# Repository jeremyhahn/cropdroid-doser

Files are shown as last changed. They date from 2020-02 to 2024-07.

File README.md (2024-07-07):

# cropdroid-doser

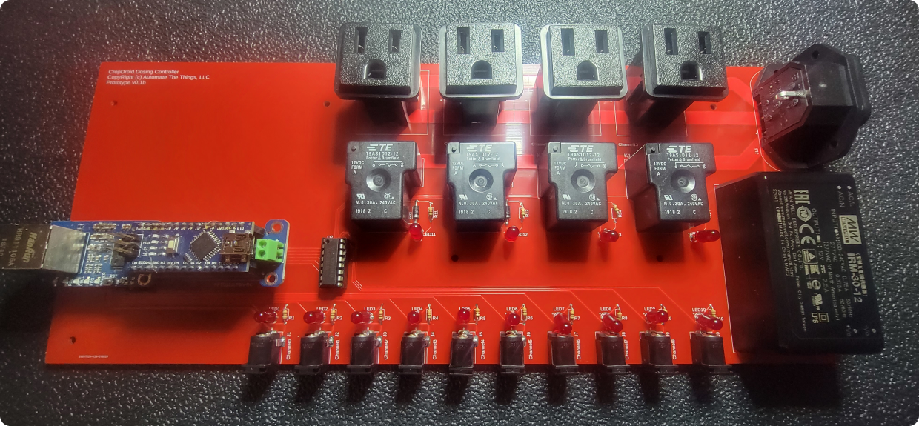
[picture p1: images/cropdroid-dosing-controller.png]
[](https://github.com/jeremyhahn/cropdroid-doser)

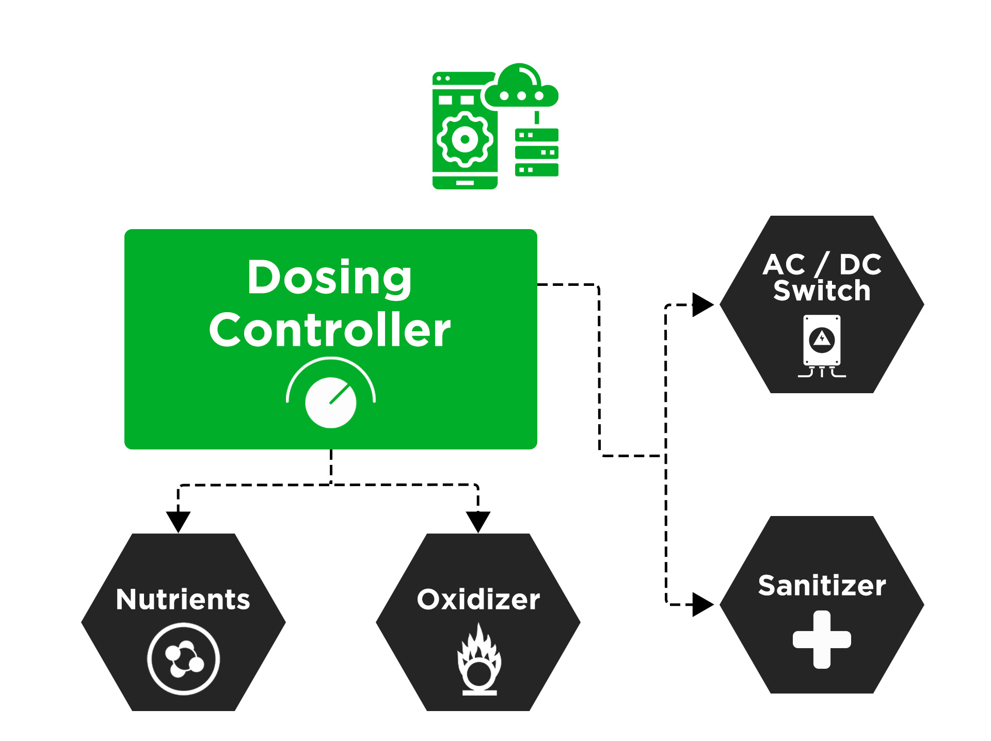
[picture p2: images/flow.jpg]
[](https://github.com/jeremyhahn/cropdroid-doser)

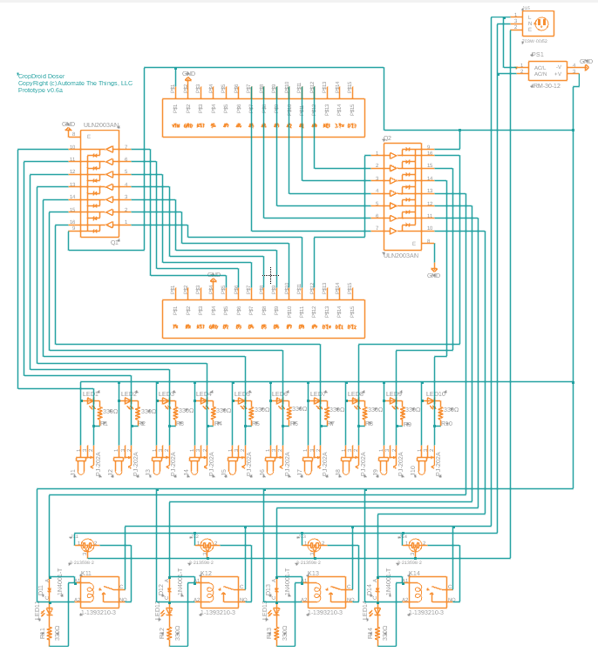
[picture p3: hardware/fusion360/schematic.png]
[](https://github.com/jeremyhahn/cropdroid-doser/blob/master/hardware/fusion360/schematic.png)

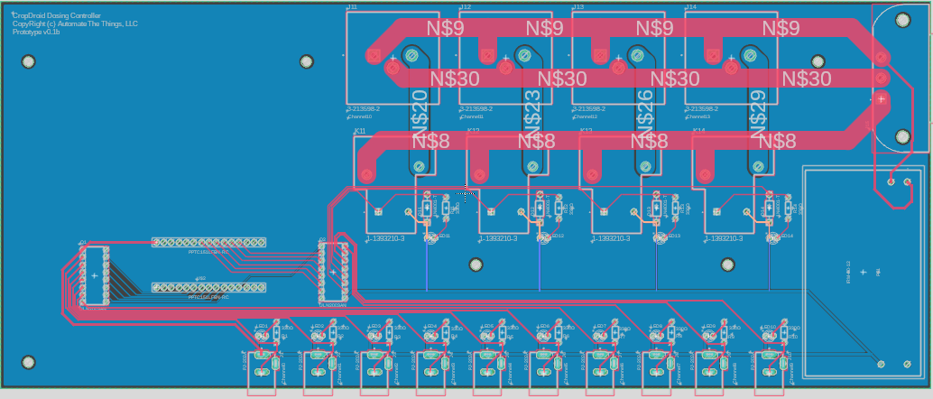
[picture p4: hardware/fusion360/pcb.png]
[](https://github.com/jeremyhahn/cropdroid-doser/blob/master/hardware/fusion360/pcb.png)

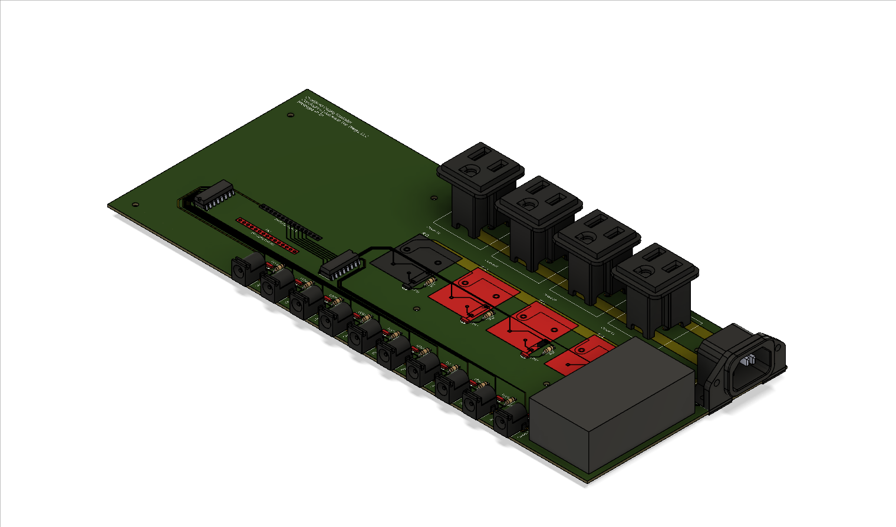
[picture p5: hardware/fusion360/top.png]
[](https://github.com/jeremyhahn/cropdroid-doser/blob/master/hardware/fusion360/top.png)

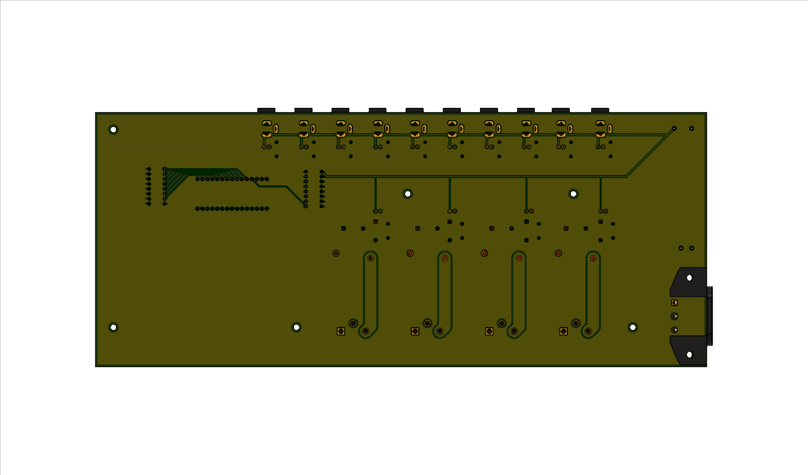
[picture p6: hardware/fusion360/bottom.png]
[](https://github.com/jeremyhahn/cropdroid-doser/blob/master/hardware/fusion360/bottom.png)

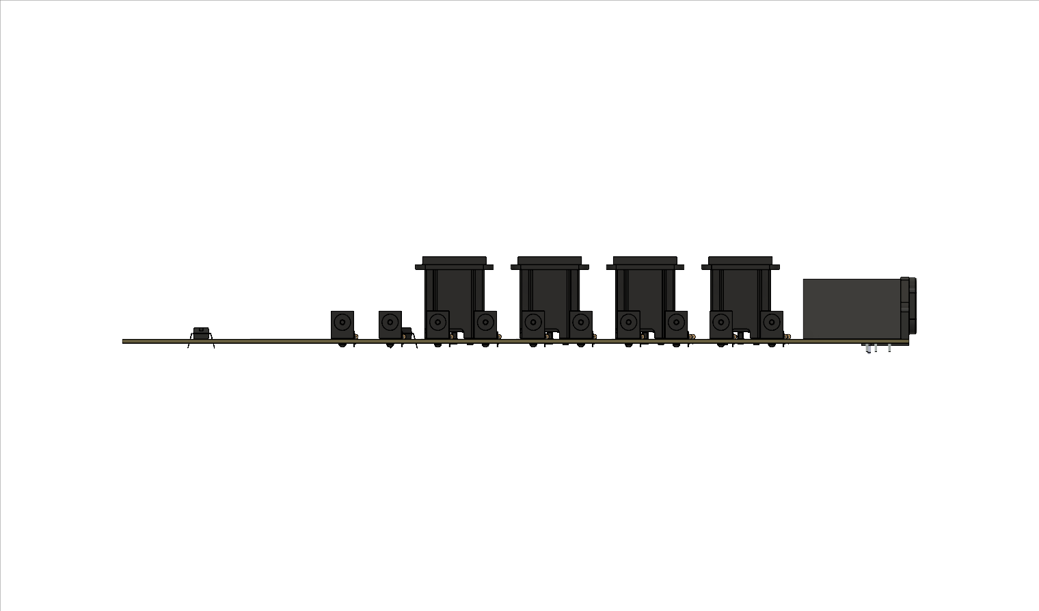
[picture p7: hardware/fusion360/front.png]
[](https://github.com/jeremyhahn/cropdroid-doser/blob/master/hardware/fusion360/front.png)

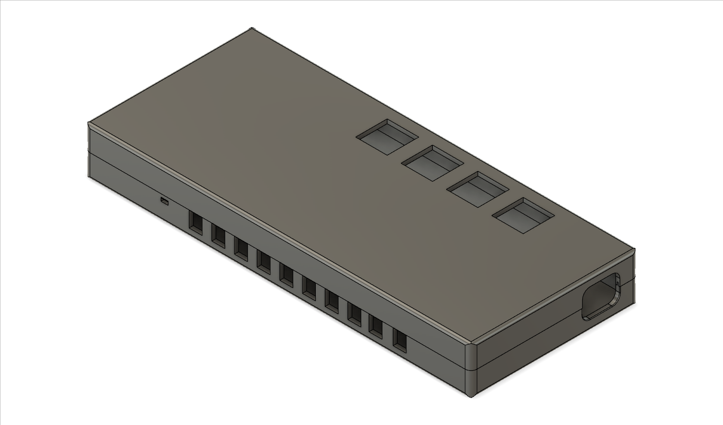
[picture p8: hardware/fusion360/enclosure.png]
[](https://github.com/jeremyhahn/cropdroid-doser/blob/master/hardware/fusion360/enclosure.png)

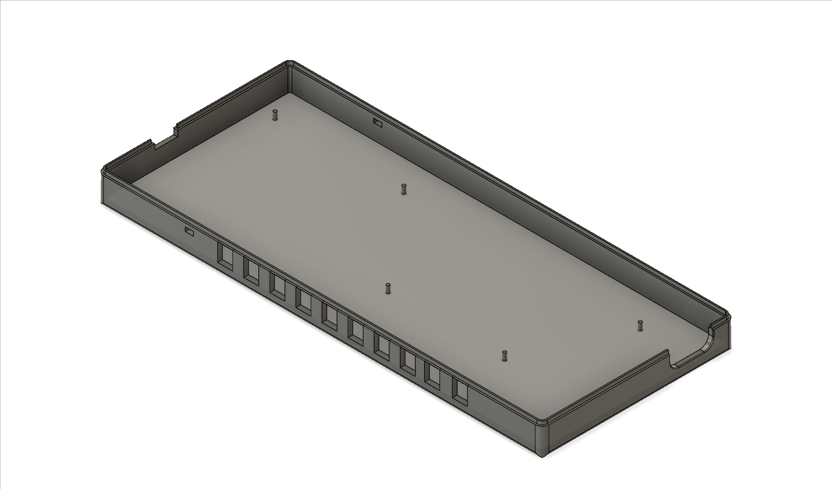
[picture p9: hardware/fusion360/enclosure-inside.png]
[](https://github.com/jeremyhahn/cropdroid-doser/blob/master/hardware/fusion360/enclosure-inside.png)

Dosing / nutrient controller for the CropDroid automation system.

# PIN Usage

## Usable

Dosing pumps can be operated on digital pins 02, 03, 05, 06, 07, 08, 09.

## Reserved

#### Serial

Arduino communicates over serial using digital pins 00 (RX) and 01 (TX).

#### Ethernet

Arduino communicates with both the W5100 and SD card using the SPI bus (through the ICSP header).

On all boards, pin 10 is used to select the W5100 and pin 4 for the SD card. 

##### Nano / Uno
Digital pins 10, 11, 12, and 13.

##### Meta
Digital pins 50, 51, and 52. 

## Support

Please consider supporting this project for ongoing success and sustainability. I'm a passionate open source contributor making a professional living creating free, secure, scalable, robust, enterprise grade, distributed systems and cloud native solutions.

I'm also available for international consulting opportunities. Please let me know how I can assist you or your organization in achieving your desired security posture and technology goals.

https://github.com/sponsors/jeremyhahn

https://www.linkedin.com/in/jeremyhahn

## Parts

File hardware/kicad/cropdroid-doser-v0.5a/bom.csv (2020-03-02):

Reference | Quantity | Value | Footprint | Datasheet | Category | DK_Datasheet_Link | DK_Detail_Page | Description | Digi-Key_PN | Family | MPN | Manufacturer | Status | Field4 | Field5 | Field6
D1 D3 D5 D7 | 4 | 1N4001 | Diode_THT:D_DO-41_SOD81_P10.16mm_Horizontal | http://www.vishay.com/docs/88503/1n4001.pdf
D2 D4 D6 D8 | 4 | LED | libraries:CAPPRD350W60D800H2000 | ~
J1 J2 J3 J4 J6 J7 J9 J10 J11 J13 | 10 | PJ-202A | digikey-footprints:Barrel_Jack_5.5mmODx2.1mmID_PJ-202A | https://www.cui.com/product/resource/digikeypdf/pj-202a.pdf | Connectors, Interconnects | https://www.cui.com/product/resource/digikeypdf/pj-202a.pdf | /product-detail/en/cui-inc/PJ-202A/CP-202A-ND/252007 | CONN PWR JACK 2X5.5MM KINKED PIN | CP-202A-ND | Barrel - Power Connectors | PJ-202A | CUI Inc. | Active
J15 | 1 | 703W-00_52 | QUALTEK_703W-00:QUALTEK_703W-00_52 | B |  |  |  |  |  |  |  |  |  | Manufacturer Recommendations | Qualtek
J5 J8 J12 J14 | 4 | 3-213598-2 | 3-213598-2:TE_3-213598-2 | https://www.te.com/usa-en/product-3-213598-2.html?te_bu=Cor&te_type=disp&elqCampaignId=32493 |  |  |  |  |  |  |  |  |  | Compliant | 3-213598-2 | Convenience Outlet
K1 K2 K3 K4 | 4 | T9AS1D12-15 | T9AS1D12-15:RELAY_T9AS1D12-15 | https://www.te.com/usa-en/product-1-1393210-4.html?te_bu=Cor&te_type=disp&elqCampaignId=32493 |  |  |  |  |  |  |  |  |  | 1-1393210-4
Q1 Q2 | 2 | ULN2003AN | digikey-footprints:DIP-16_W7.62mm | http://www.ti.com/general/docs/suppproductinfo.tsp?distId=10 | Discrete Semiconductor Products | http://www.ti.com/general/docs/suppproductinfo.tsp?distId=10 | /product-detail/en/texas-instruments/ULN2003AN/296-1979-5-ND/277624 | IC PWR RELAY 7NPN 1:1 16DIP | 296-1979-5-ND | Transistors - Bipolar (BJT) - Arrays | ULN2003AN | Texas Instruments | Active
R1 R2 R3 R4 | 4 | R | Resistor_THT:R_Axial_DIN0207_L6.3mm_D2.5mm_P10.16mm_Horizontal | ~
U2 U1 | 2 | PPTC151LFBN-RC | PPTC151LFBN-RC:PPTC151LFBN-RC
U3 | 1 | IRM-30-12 | IRM-30-12:IRM-30-12

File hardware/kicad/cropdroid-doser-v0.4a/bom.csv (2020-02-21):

Reference | Quantity | Value | Footprint | Datasheet | Category | DK_Datasheet_Link | DK_Detail_Page | Description | Digi-Key_PN | Family | MPN | Manufacturer | Status | Field4 | Field5 | Field6
CON1 CON2 CON3 CON5 CON6 CON8 CON9 CON10 CON4 CON7 | 10 | SJ1-3523N | digikey-footprints:Headphone_Jack_3.5mm_SJ1-3523N | https://www.cui.com/product/resource/digikeypdf/sj1-352xn_series.pdf | Connectors, Interconnects | https://www.cui.com/product/resource/digikeypdf/sj1-352xn_series.pdf | /product-detail/en/cui-inc/SJ1-3523N/CP1-3523N-ND/738689 | CONN JACK STEREO 3.5MM R/A | CP1-3523N-ND | Barrel - Audio Connectors | SJ1-3523N | CUI Inc. | Active
D1 D3 D5 D7 | 4 | 1N4001 | Diode_THT:D_DO-41_SOD81_P10.16mm_Horizontal | http://www.vishay.com/docs/88503/1n4001.pdf
D2 D4 D6 D8 | 4 | LED | libraries:CAPPRD350W60D800H2000 | ~
J1 J2 J3 J4 | 4 | 3-213598-2 | 3-213598-2:TE_3-213598-2 | https://www.te.com/usa-en/product-3-213598-2.html?te_bu=Cor&te_type=disp&elqCampaignId=32493 |  |  |  |  |  |  |  |  |  | Compliant | 3-213598-2 | Convenience Outlet
J5 | 1 | 703W-00_52 | QUALTEK_703W-00:QUALTEK_703W-00_52 | B |  |  |  |  |  |  |  |  |  | Manufacturer Recommendations | Qualtek
K1 K2 K3 K4 | 4 | T9AS1D12-15 | T9AS1D12-15:RELAY_T9AS1D12-15 | https://www.te.com/usa-en/product-1-1393210-4.html?te_bu=Cor&te_type=disp&elqCampaignId=32493 |  |  |  |  |  |  |  |  |  | 1-1393210-4
Q1 Q2 | 2 | ULN2003AN | digikey-footprints:DIP-16_W7.62mm | http://www.ti.com/general/docs/suppproductinfo.tsp?distId=10 | Discrete Semiconductor Products | http://www.ti.com/general/docs/suppproductinfo.tsp?distId=10 | /product-detail/en/texas-instruments/ULN2003AN/296-1979-5-ND/277624 | IC PWR RELAY 7NPN 1:1 16DIP | 296-1979-5-ND | Transistors - Bipolar (BJT) - Arrays | ULN2003AN | Texas Instruments | Active
R1 R2 R3 R4 | 4 | R | Resistor_THT:R_Axial_DIN0207_L6.3mm_D2.5mm_P10.16mm_Horizontal | ~
U2 U1 | 2 | PPTC151LFBN-RC | PPTC151LFBN-RC
U3 | 1 | IRM-30-12 | IRM-30-12:IRM-30-12

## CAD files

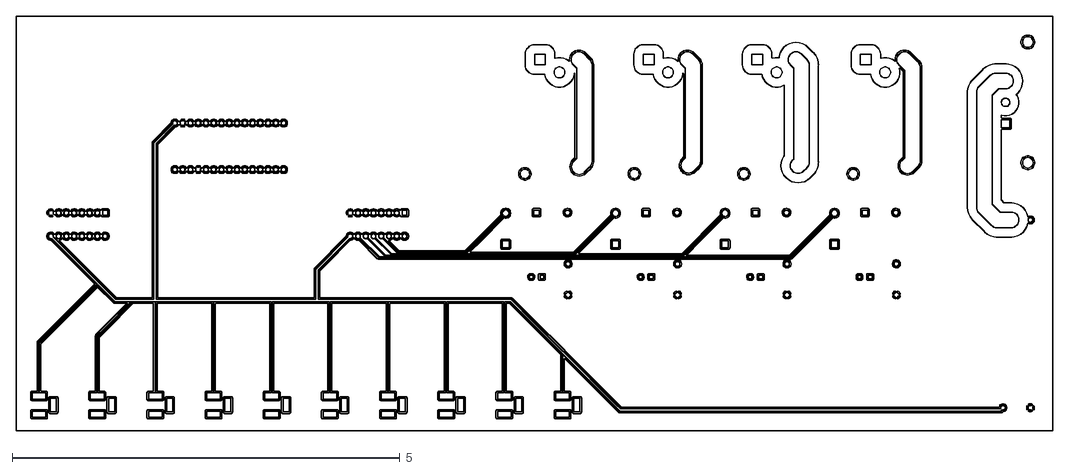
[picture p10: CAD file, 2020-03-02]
hardware/kicad/cropdroid-doser-v0.5a/plots/dxf/cropdroid-doser-B_Cu.dxf
13.4 x 5.35

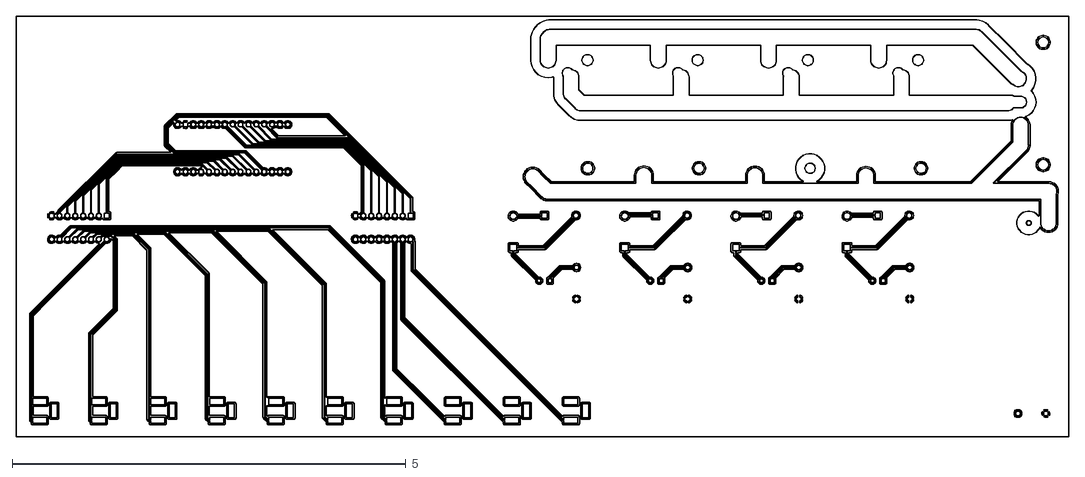
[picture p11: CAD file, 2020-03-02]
hardware/kicad/cropdroid-doser-v0.5a/plots/dxf/cropdroid-doser-F_Cu.dxf
13.4 x 5.35

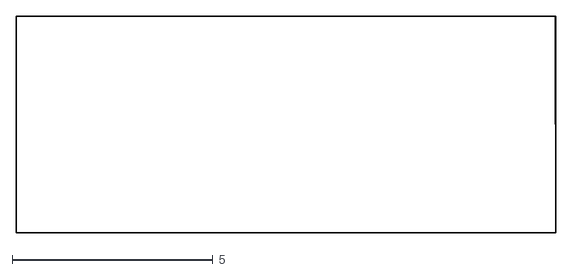
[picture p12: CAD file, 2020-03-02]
hardware/kicad/cropdroid-doser-v0.5a/plots/dxf/cropdroid-doser-Edge_Cuts.dxf
13.4 x 5.39

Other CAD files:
hardware/kicad/cropdroid-doser-v0.5a/plots/dxf/cropdroid-doser-B_Mask.dxf
hardware/kicad/cropdroid-doser-v0.5a/plots/dxf/cropdroid-doser-B_Paste.dxf
hardware/kicad/cropdroid-doser-v0.5a/plots/dxf/cropdroid-doser-B_SilkS.dxf
hardware/kicad/cropdroid-doser-v0.5a/plots/dxf/cropdroid-doser-F_Mask.dxf
hardware/kicad/cropdroid-doser-v0.5a/plots/dxf/cropdroid-doser-F_Paste.dxf
hardware/kicad/cropdroid-doser-v0.5a/plots/dxf/cropdroid-doser-F_SilkS.dxf

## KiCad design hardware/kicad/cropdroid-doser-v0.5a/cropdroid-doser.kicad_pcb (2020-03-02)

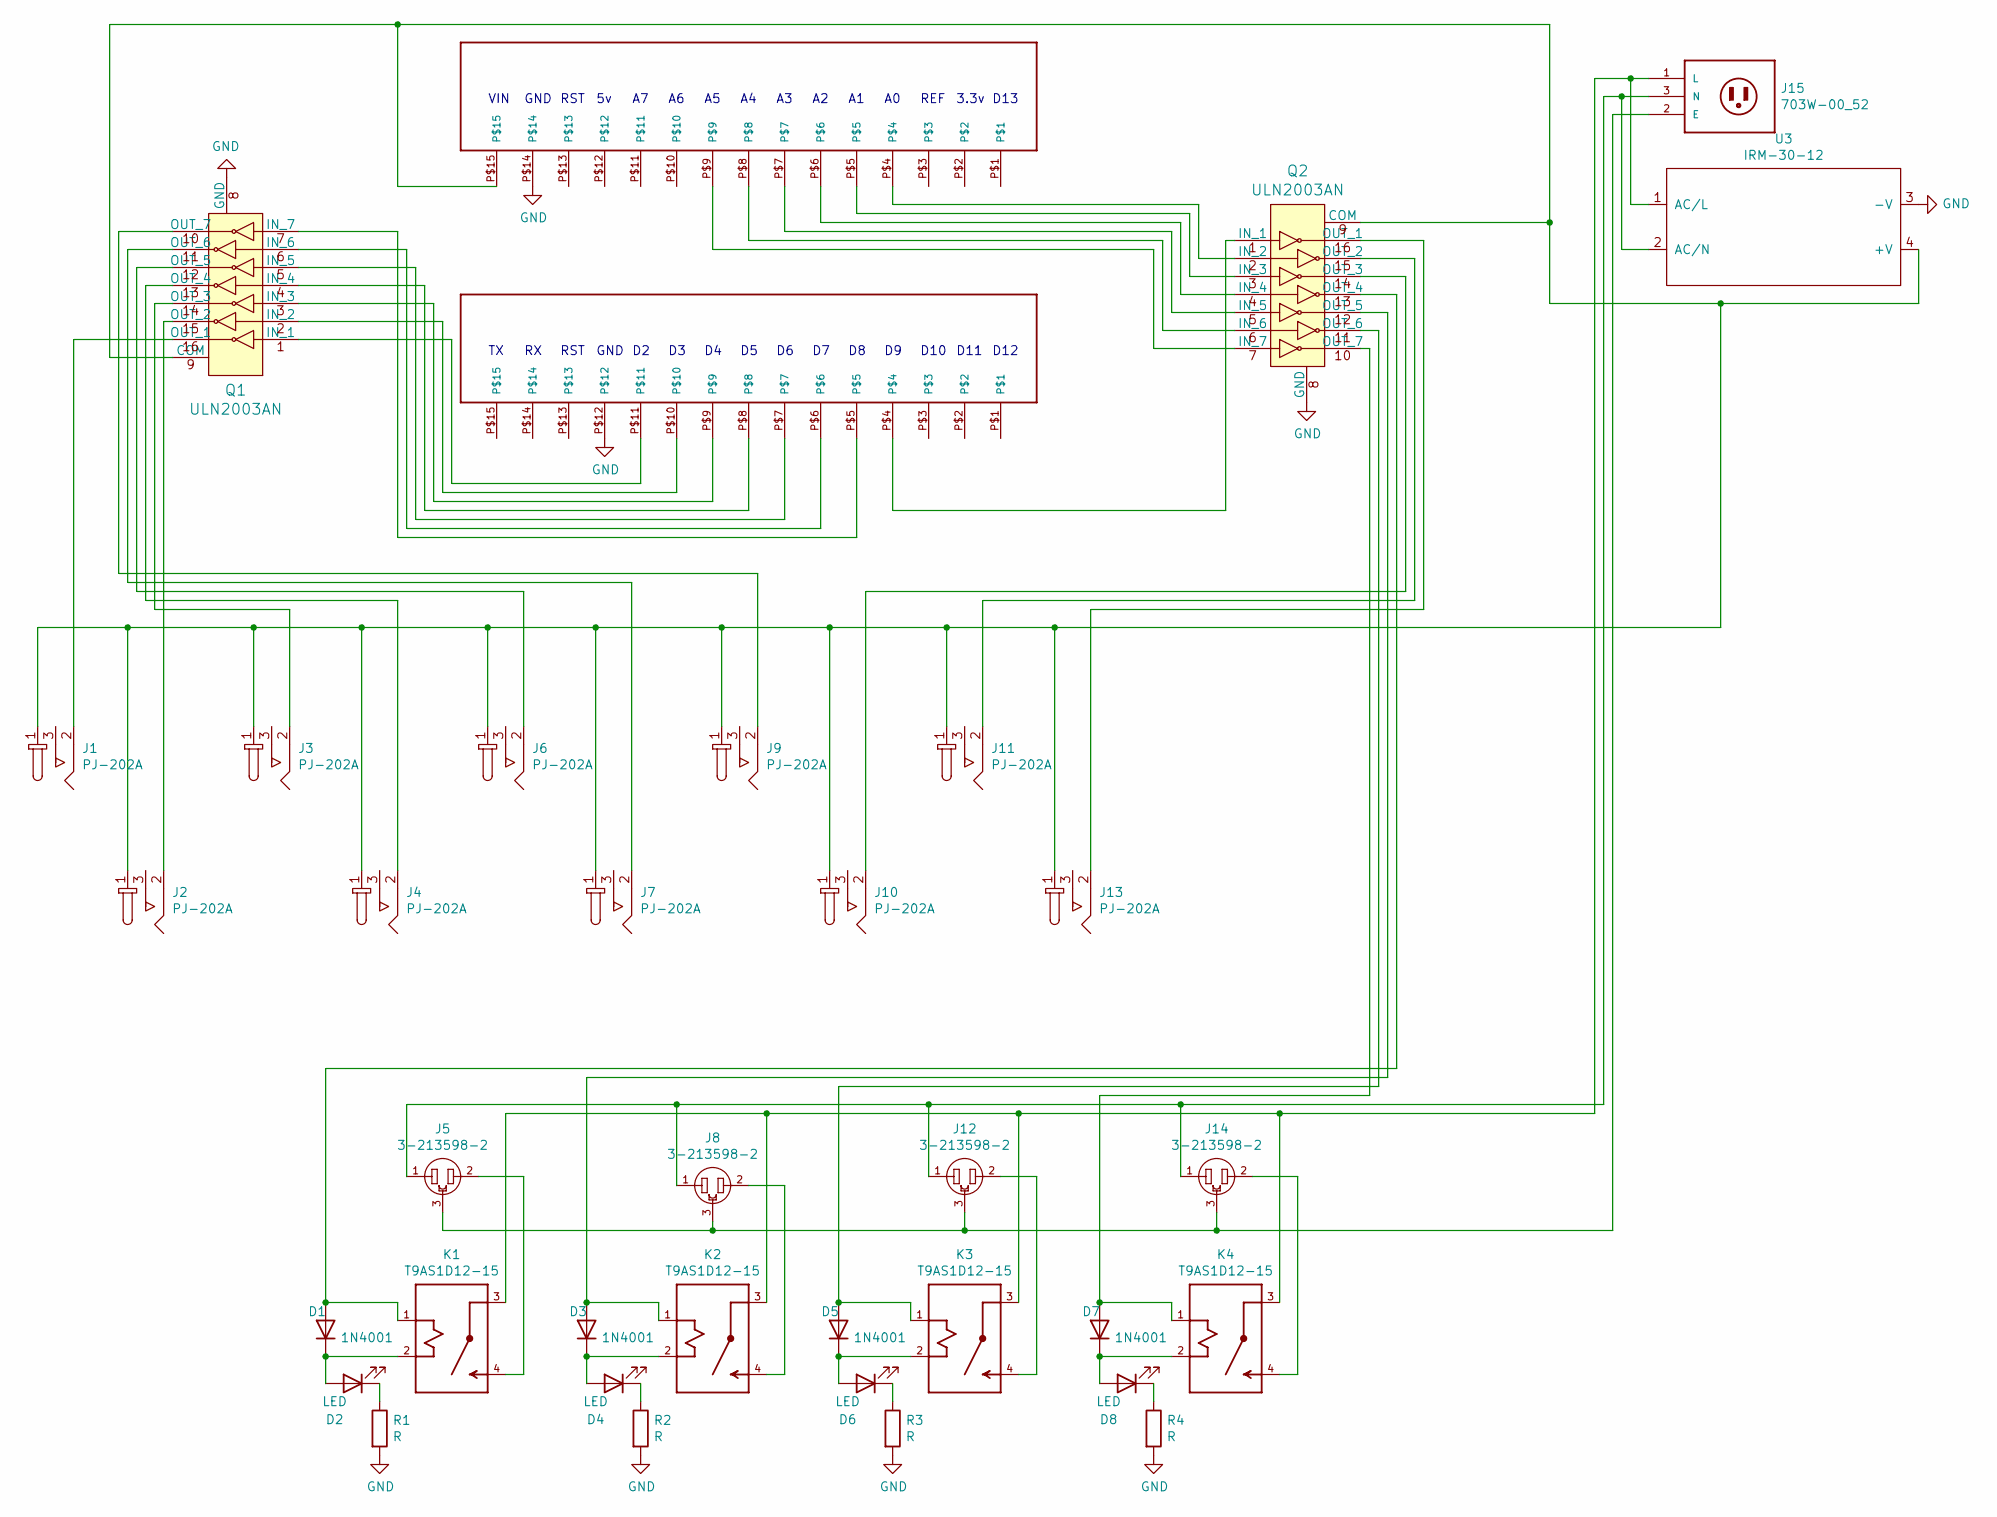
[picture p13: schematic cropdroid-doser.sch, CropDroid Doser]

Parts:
D1, D3, D5, D7: 1N4001; D_DO-41_SOD81_P10.16mm_Horizontal
D2, D4, D6, D8: LED; CAPPRD350W60D800H2000
J1, J2, J3, J4, J6, J7, J9, J10, J11, J13: PJ-202A; Barrel_Jack_5.5mmODx2.1mmID_PJ-202A; MPN PJ-202A; Digi-Key_PN CP-202A-ND
J5, J8, J12, J14: 3-213598-2; TE_3-213598-2
J15: 703W-00_52; QUALTEK_703W-00_52
K1, K2, K3, K4: T9AS1D12-15; RELAY_T9AS1D12-15
Q1, Q2: ULN2003AN; DIP-16_W7.62mm; MPN ULN2003AN; Digi-Key_PN 296-1979-5-ND
R1, R2, R3, R4: R; R_Axial_DIN0207_L6.3mm_D2.5mm_P10.16mm_Horizontal
U1, U2: PPTC151LFBN-RC
U3: IRM-30-12

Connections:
GND: Q1.8 (GND), Q2.8 (GND), R1.2, R2.2, R3.2, R4.2, U1.P$14, U2.P$12, U3.3 (-V)
unnamed: D1.1 (K), D2.2 (A), K1.2 (A2)
unnamed: D1.2 (A), K1.1 (A1), Q2.13 (OUT_4)
unnamed: D2.1 (K), R1.1
unnamed: D3.1 (K), D4.2 (A), K2.2 (A2)
unnamed: D3.2 (A), K2.1 (A1), Q2.12 (OUT_5)
unnamed: D4.1 (K), R2.1
unnamed: D5.1 (K), D6.2 (A), K3.2 (A2)
unnamed: D5.2 (A), K3.1 (A1), Q2.11 (OUT_6)
unnamed: D6.1 (K), R3.1
unnamed: D7.1 (K), D8.2 (A), K4.2 (A2)
unnamed: D7.2 (A), K4.1 (A1), Q2.10 (OUT_7)
unnamed: D8.1 (K), R4.1
unnamed: J1.1, J2.1, J3.1, J4.1, J6.1, J7.1, J9.1, J10.1, J11.1, J13.1, Q1.9 (COM), Q2.9 (COM), U1.P$15, U3.4 (+V)
unnamed: J1.2, Q1.16 (OUT_1)
unnamed: J2.2, Q1.15 (OUT_2)
unnamed: J3.2, Q1.14 (OUT_3)
unnamed: J4.2, Q1.13 (OUT_4)
unnamed: J5.2, K1.4 (NO)
unnamed: J6.2, Q1.12 (OUT_5)
unnamed: J7.2, Q1.11 (OUT_6)
unnamed: J8.2, K2.4 (NO)
unnamed: J9.2, Q1.10 (OUT_7)
unnamed: J10.2, Q2.14 (OUT_3)
unnamed: J11.2, Q2.15 (OUT_2)
unnamed: J5.1, J8.1, J12.1, J14.1, J15.3 (N), U3.2 (AC/N)
unnamed: J12.2, K3.4 (NO)
unnamed: J5.3, J8.3, J12.3, J14.3, J15.2 (E)
unnamed: J13.2, Q2.16 (OUT_1)
unnamed: J14.2, K4.4 (NO)
unnamed: J15.1 (L), K1.3 (C), K2.3 (C), K3.3 (C), K4.3 (C), U3.1 (AC/L)
unnamed: Q1.1 (IN_1), U2.P$11
unnamed: Q1.2 (IN_2), U2.P$10
unnamed: Q1.3 (IN_3), U2.P$9
unnamed: Q1.4 (IN_4), U2.P$8
unnamed: Q1.5 (IN_5), U2.P$7
unnamed: Q1.6 (IN_6), U2.P$6
unnamed: Q1.7 (IN_7), U2.P$5
unnamed: Q2.1 (IN_1), U2.P$4
unnamed: Q2.2 (IN_2), U1.P$4
unnamed: Q2.3 (IN_3), U1.P$5
unnamed: Q2.4 (IN_4), U1.P$6
unnamed: Q2.5 (IN_5), U1.P$7
unnamed: Q2.6 (IN_6), U1.P$8
unnamed: Q2.7 (IN_7), U1.P$9

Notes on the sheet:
RST
GND
D10
D11
D12
VIN
REF
3.3v
D13

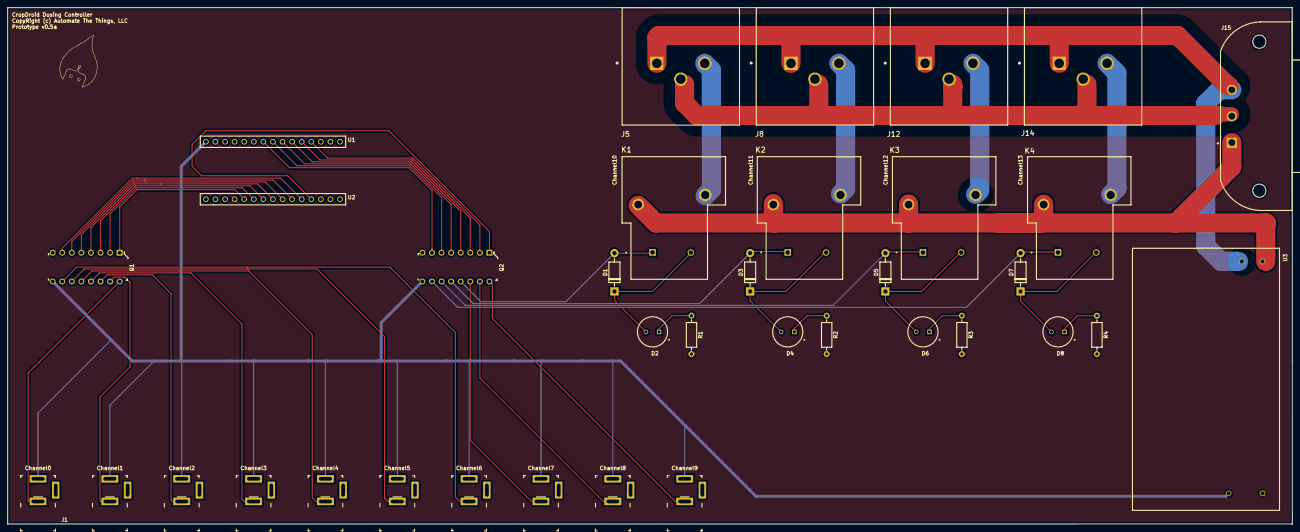
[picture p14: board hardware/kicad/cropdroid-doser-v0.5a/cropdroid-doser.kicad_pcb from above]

Board: 2 copper layers, 340.7 x 136.9 mm, 36 parts (0 on the bottom side), 45 nets.

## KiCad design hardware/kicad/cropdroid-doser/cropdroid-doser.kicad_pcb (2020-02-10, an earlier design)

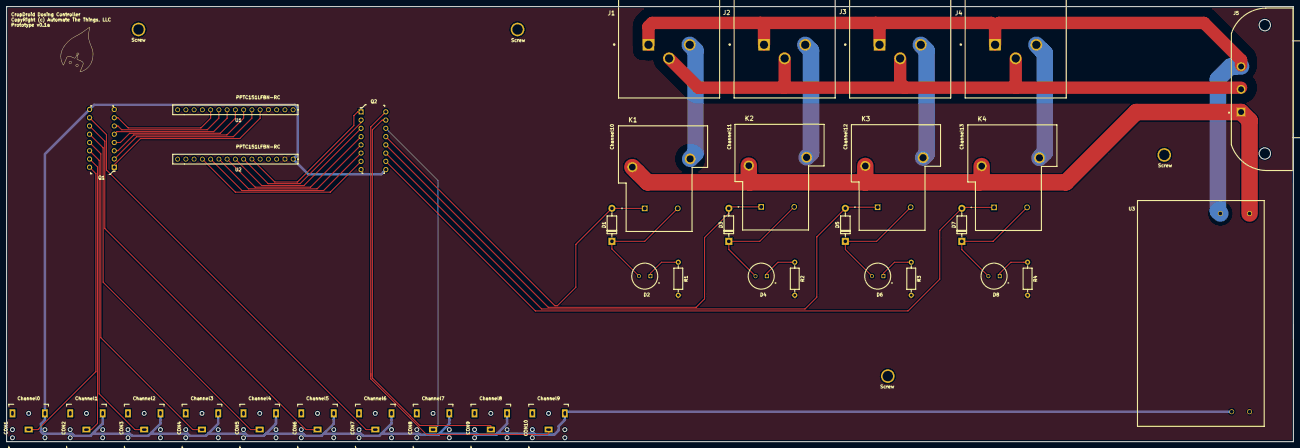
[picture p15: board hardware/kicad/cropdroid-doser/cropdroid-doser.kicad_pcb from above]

Board: 2 copper layers, 396.1 x 133.9 mm, 40 parts (0 on the bottom side), 45 nets.

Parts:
CON1, CON2, CON3, CON4, CON5, CON6, CON7, CON8, CON9, CON10: SJ1-3523N; Headphone_Jack_3.5mm_SJ1-3523N
D1, D3, D5, D7: 1N4001; D_DO-41_SOD81_P10.16mm_Horizontal
D2, D4, D6, D8: LED; CAPPRD350W60D800H2000
J1, J2, J3, J4: 3-213598-2; TE_3-213598-2
J5: 703W-00_52; QUALTEK_703W-00_52
K1, K2, K3, K4: T9AS1D12-15; RELAY_T9AS1D12-15
Q1, Q2: ULN2003AN; DIP-16_W7.62mm
R1, R2, R3, R4: R; R_Axial_DIN0207_L6.3mm_D2.5mm_P10.16mm_Horizontal
Screw: Drill; Drill_Hole
Screw#2, Screw#3, Screw#4: Drill; Drill_Hole
U1, U2: PPTC151LFBN-RC
U3: IRM-30-12

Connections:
GND: Q1.8, Q2.8, R1.2, R2.2, R3.2, R4.2, U1.P$4, U2.P$2, U3.3
unnamed: CON1.1, Q1.16
unnamed: CON1.2, CON2.2, CON3.2, CON4.2, CON5.2, CON6.2, CON7.2, CON8.2, CON9.2, CON10.2, Q1.9, Q2.9, U2.P$1, U3.4
unnamed: CON2.1, Q1.15
unnamed: CON3.1, Q1.14
unnamed: CON4.1, Q1.13
unnamed: CON5.1, Q1.12
unnamed: CON6.1, Q1.11
unnamed: CON7.1, Q1.10
unnamed: CON8.1, Q2.14
unnamed: CON9.1, Q2.15
unnamed: CON10.1, Q2.16
unnamed: D1.1, D2.2, K1.2
unnamed: D1.2, K1.1, Q2.13
unnamed: D2.1, R1.1
unnamed: D3.1, D4.2, K2.2
unnamed: D3.2, K2.1, Q2.12
unnamed: D4.1, R2.1
unnamed: D5.1, D6.2, K3.2
unnamed: D5.2, K3.1, Q2.11
unnamed: D6.1, R3.1
unnamed: D7.1, D8.2, K4.2
unnamed: D7.2, K4.1, Q2.10
unnamed: D8.1, R4.1
unnamed: J1.1, J2.1, J3.1, J4.1, J5.3, U3.2
unnamed: J1.2, K1.4
unnamed: J1.3, J2.3, J3.3, J4.3, J5.2
unnamed: J2.2, K2.4
unnamed: J3.2, K3.4
unnamed: J4.2, K4.4
unnamed: J5.1, K1.3, K2.3, K3.3, K4.3, U3.1
unnamed: Q1.1, U1.P$5
unnamed: Q1.2, U1.P$6
unnamed: Q1.3, U1.P$7
unnamed: Q1.4, U1.P$8
unnamed: Q1.5, U1.P$9
unnamed: Q1.6, U1.P$10
unnamed: Q1.7, U1.P$11
unnamed: Q2.1, U2.P$6
unnamed: Q2.2, U2.P$7
unnamed: Q2.3, U2.P$8
unnamed: Q2.4, U2.P$9
unnamed: Q2.5, U2.P$10
unnamed: Q2.6, U2.P$11
unnamed: Q2.7, U2.P$12

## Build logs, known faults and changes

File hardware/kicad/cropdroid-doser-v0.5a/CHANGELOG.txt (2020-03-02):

v0.5a
- Replace audio jacks with dc barrel jacks
- Space dc barrel jacks 3/4" apart

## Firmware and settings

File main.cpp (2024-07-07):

// SPDX-License-Identifier: AGPL-3.0-or-later
// SPDX-License-Identifier: commercial

#include <Arduino.h>
#include <Ethernet.h>
#include <stdlib.h>
#include "EEPROM.h"

#define DEBUG 0
#define EEPROM_DEBUG 1
#define BUFSIZE 255
#define CHANNEL_SIZE 14

extern int  __bss_end;
extern int  *__brkval;

const char json_bracket_open[] = "{";
const char json_bracket_close[] = "}";
const char json_array_bracket_close[] = "]";
const char json_comma[] = ",";

const char string_initializing[] PROGMEM = "Initializing dosing controller...";
const char string_dhcp_failed[] PROGMEM = "DHCP Failed";
const char string_http_200[] PROGMEM = "HTTP/1.1 200 OK";
const char string_http_404[] PROGMEM = "HTTP/1.1 404 Not Found";
const char string_http_500[] PROGMEM = "HTTP/1.1 500 Internal Server Error";
const char string_http_content_type_json[] PROGMEM = "Content-Type: application/json";
const char string_http_xpowered_by[] PROGMEM = "X-Powered-By: CropDroid v1.0";
const char string_rest_address[] PROGMEM = "REST service listening on: ";
const char string_switch_on[] PROGMEM = "Switching on";
const char string_switch_off[] PROGMEM = "Switching off";
const char string_json_key_mem[] PROGMEM = "\"mem\":";
const char string_json_key_uptime[] PROGMEM = ",\"uptime\":";
const char string_json_key_metrics[] PROGMEM = "\"metrics\":{";
const char string_json_key_channels[] PROGMEM = ",\"channels\":[";
const char string_json_key_channel[] PROGMEM = "\"channel\":";
const char string_json_key_pin[] PROGMEM = ",\"pin\":";
const char string_json_key_position[] PROGMEM =  ",\"position\":";
const char string_json_key_value[] PROGMEM =  ",\"value\":";
const char string_json_key_address[] PROGMEM =  "\"address\":";
const char string_json_key_bracket_open[] PROGMEM = "{";
const char string_json_key_bracket_close[] PROGMEM = "}";
const char string_json_error_invalid_channel[] PROGMEM = "\"error\":\"Invalid channel\"";
const char string_json_reboot_true PROGMEM = "\"reboot\":true";
const char string_json_reset_true PROGMEM = "\"reset\":true";
const char string_hardware_version[] PROGMEM = "\"hardware\":\"doser-v0.1b\",";
const char string_firmware_version[] PROGMEM = "\"firmware\":\"1.0.0b\"";
const char * const string_table[] PROGMEM = {
  string_initializing,
  string_dhcp_failed,
  string_http_200,
  string_http_404,
  string_http_500,
  string_http_content_type_json,
  string_http_xpowered_by,
  string_rest_address,
  string_switch_on,
  string_switch_off,
  string_json_key_mem,
  string_json_key_uptime,
  string_json_key_metrics,
  string_json_key_channels,
  string_json_key_channel,
  string_json_key_pin,
  string_json_key_position,
  string_json_key_value,
  string_json_key_address,
  string_json_key_bracket_open,
  string_json_key_bracket_close,
  string_json_error_invalid_channel,
  string_json_reboot_true,
  string_json_reset_true,
  string_hardware_version,
  string_firmware_version
};
int idx_initializing = 0,
    idx_dhcp_failed = 1,
	idx_http_200 = 2,
	idx_http_404 = 3,
	idx_http_500 = 4,
	idx_http_content_type_json = 5,
	idx_http_xpowered_by = 6,
	idx_rest_address = 7,
	idx_switch_on = 8,
	idx_switch_off = 9,
	idx_json_key_mem = 10,
	idx_json_key_uptime = 11,
	idx_json_key_metrics = 12,
	idx_json_key_channels = 13,
	idx_json_key_channel = 14,
	idx_json_key_pin = 15,
	idx_json_key_position = 16,
	idx_json_key_value = 17,
	idx_json_key_address = 18,
	idx_json_key_bracket_open = 19,
	idx_json_key_bracket_close = 20,
	idx_json_error_invalid_channel = 21,
	idx_json_reboot_true = 22,
	idx_json_reset_true = 23,
	idx_hardware_version = 24,
	idx_firmware_version = 25;
char string_buffer[50];
char float_buffer[10];

void handleWebRequest();
void switchOn(int pin);
void switchOff(int pin);
void send404();
void resetDefaults();
int availableMemory();
void(* resetFunc) (void) = 0;

byte defaultMac[] = { 0x04, 0x02, 0x00, 0x00, 0x00, 0x03 };

byte mac[] = {
	EEPROM.read(0),
	EEPROM.read(1),
	EEPROM.read(2),
	EEPROM.read(3),
	EEPROM.read(4),
	EEPROM.read(5)
};
IPAddress ip(
  EEPROM.read(6),
  EEPROM.read(7),
  EEPROM.read(8),
  EEPROM.read(9));

EthernetServer httpServer(80);
EthernetClient httpClient;

const int NULL_CHANNEL = 255;
const uint8_t channels[CHANNEL_SIZE] = {
	2, 3, 4, 5, 6, 7, 8, 9,
	A0, A1, A2, A3, A4, A5
};
unsigned long channel_table[CHANNEL_SIZE][3] = {
	// channel, start, interval
   {NULL_CHANNEL, 0, 0},
   {NULL_CHANNEL, 0, 0},
   {NULL_CHANNEL, 0, 0},
   {NULL_CHANNEL, 0, 0},
   {NULL_CHANNEL, 0, 0},
   {NULL_CHANNEL, 0, 0},
   {NULL_CHANNEL, 0, 0},
   {NULL_CHANNEL, 0, 0},
   {NULL_CHANNEL, 0, 0},
   {NULL_CHANNEL, 0, 0},
   {NULL_CHANNEL, 0, 0},
   {NULL_CHANNEL, 0, 0},
   {NULL_CHANNEL, 0, 0},
   {NULL_CHANNEL, 0, 0} // 14
};

int main(void) {
  init();
  setup();;

  for (;;)
    loop();

  return 0;
}

void setup(void) {

  //EEPROM.write(0, 255);

  #if DEBUG || EEPROM_DEBUG
	Serial.begin(115200);

	strcpy_P(string_buffer, (char*)pgm_read_word(&(string_table[idx_initializing])));
	Serial.println(string_buffer);
  #endif

  analogReference(DEFAULT);

  for(int i=0; i<CHANNEL_SIZE; i++) {
    pinMode(channels[i], OUTPUT);
    digitalWrite(channels[i], LOW);
  }

  byte macByte1 = EEPROM.read(0);

  #if DEBUG || EEPROM_DEBUG
	Serial.print("macByte1: ");
	Serial.println(macByte1);
  #endif

  if(macByte1 == 255) {
	resetDefaults();
	if(Ethernet.begin(defaultMac) == 0) {
	  #if DEBUG
		strcpy_P(string_buffer, (char*)pgm_read_word(&(string_table[idx_dhcp_failed])));
		Serial.println(string_buffer);
	  #endif
	  return;
	}
  }
  else {
	Ethernet.begin(mac, ip);
  }

  #if DEBUG || EEPROM_DEBUG
	Serial.print("MAC: ");
	for(int i=0; i<6; i++) {
	  Serial.print(mac[i], HEX);
	}
	Serial.println();

	strcpy_P(string_buffer, (char*)pgm_read_word(&(string_table[idx_rest_address])));
	Serial.print(string_buffer);
	Serial.println(Ethernet.localIP());
  #endif

  httpServer.begin();
}

void loop() {
  handleWebRequest();
  delay(100);
}

void switchOn(int pin) {
#if DEBUG
  char sPin[3];
  itoa(pin, sPin, 10);
  strcpy_P(string_buffer, (char*)pgm_read_word(&(string_table[idx_switch_on])));
  strcat(string_buffer, " pin ");
  strcat(string_buffer, sPin);
  Serial.println(string_buffer);
#endif
  digitalWrite(pin, HIGH);
}

void switchOff(int pin) {
#if DEBUG
  char sPin[3];
  itoa(pin, sPin, 10);
  strcpy_P(string_buffer, (char*)pgm_read_word(&(string_table[idx_switch_off])));
  strcat(string_buffer, " pin ");
  strcat(string_buffer, sPin);
  Serial.println(string_buffer);
#endif
  digitalWrite(pin, LOW);
}

void handleWebRequest() {

	unsigned long currentMillis = millis();

	for(int i=0; i<CHANNEL_SIZE; i++) {
		if(channel_table[i][0] != NULL_CHANNEL) {
			if(currentMillis - channel_table[i][1] > channel_table[i][2]) {

				digitalWrite(channel_table[i][0], LOW);

				#if DEBUG
				  Serial.print("Turning channel ");
				  Serial.print(i);
				  Serial.print(" (pin ");
				  Serial.print(channel_table[i][0]);
				  Serial.print(") off after ");
				  Serial.print(channel_table[i][2] / 1000);
				  Serial.println(" seconds");
				#endif

				channel_table[i][0] = NULL_CHANNEL;
				channel_table[i][1] = 0;
				channel_table[i][2] = 0;
			}
		}
	}

	httpClient = httpServer.available();

	char clientline[BUFSIZE] = {0};
	int index = 0;

	bool reboot = false;
	char json[275];
	char sPin[3];
	char state[3];

	if (httpClient) {

		// reset input buffer
		index = 0;

		while (httpClient.connected()) {

			if (httpClient.available()) {

				char c = httpClient.read();
				if (c != '\n' && c != '\r' && index < BUFSIZE) {
					clientline[index++] = c;
					continue;
				}

				httpClient.flush();

				String urlString = String(clientline);
				String op = urlString.substring(0, urlString.indexOf(' '));
				urlString = urlString.substring(urlString.indexOf('/'), urlString.indexOf(' ', urlString.indexOf('/')));
				urlString.toCharArray(clientline, BUFSIZE);

			    char *resource = strtok(clientline, "/");
				char *param1 = strtok(NULL, "/");
				char *param2 = strtok(NULL, "/");

				#if DEBUG
				  Serial.print("Resource: ");
				  Serial.println(resource);

				  Serial.print("Param1: ");
				  Serial.println(param1);

				  Serial.print("Param2: ");
				  Serial.println(param2);
				#endif

				// /state
				if (strncmp(resource, "state", 5) == 0) {

					strcpy(json, json_bracket_open);

					  strcpy_P(string_buffer, (char*)pgm_read_word(&(string_table[idx_json_key_metrics])));
					  strcat(json, string_buffer);

					    strcpy_P(string_buffer, (char*)pgm_read_word(&(string_table[idx_json_key_mem])));
					    strcat(json, string_buffer);
					    itoa(availableMemory(), float_buffer, 10);
					    strcat(json, float_buffer);

					  strcat(json, json_bracket_close);

					  strcpy_P(string_buffer, (char*)pgm_read_word(&(string_table[idx_json_key_channels])));
					  strcat(json, string_buffer);
						for(int i=0; i<CHANNEL_SIZE; i++) {
						  itoa(digitalRead(channels[i]), state, 10);
						  strcat(json, state);
						  if(i + 1 < CHANNEL_SIZE) {
						    strcat(json, ",");
						  }
						}
				      strcat(json, json_array_bracket_close);

					strcat(json, json_bracket_close);
				}

				// /eeprom
				else if (strncmp(resource, "eeprom", 6) == 0) {

					#if EEPROM_DEBUG
						Serial.println("/eeprom");
						Serial.println(param1);
						Serial.println(param2);
					#endif

					EEPROM.write(atoi(param1), atoi(param2));

					strcpy(json, json_bracket_open);

					  strcpy_P(string_buffer, (char*)pgm_read_word(&(string_table[idx_json_key_address])));
					  strcat(json, string_buffer);
					  strcat(json, param1);

					  strcpy_P(string_buffer, (char*)pgm_read_word(&(string_table[idx_json_key_value])));
					  strcat(json, string_buffer);
					  strcat(json, param2);

					strcat(json, json_bracket_close);
				}

				// /timer/{channel}/{seconds}
				else if (strncmp(resource, "timer", 5) == 0) {

					if(param1 == NULL || param1 == "") {
						Serial.println("parameter required");
						//send500("parameter required");
						break;
					}

					int channel = atoi(param1);
					unsigned long duration = strtoul(param2, NULL, 10);

					if(channel >= 0 && channel < CHANNEL_SIZE && duration > 0) {

						#if DEBUG
						  Serial.print("Channel: ");
						  Serial.println(channel);

						  Serial.print("Duration: ");
                          Serial.println(duration);
						#endif

						channel_table[channel][0] = channels[channel];
						channel_table[channel][1] = millis();
						channel_table[channel][2] = duration * 1000;

						digitalWrite(channels[channel], HIGH);
					}
                    else {
					  #if DEBUG
					    Serial.println("Invalid channel/duration");
					  #endif
					}

					strcpy(json, json_bracket_open);

						strcat(json, "\"channel\":");
						itoa(channel, float_buffer, 10);
						strcat(json, float_buffer);

						strcat(json, ",\"duration\":");
						itoa(duration, float_buffer, 10);
						strcat(json, float_buffer);

					strcat(json, json_bracket_close);
				}

				// /switch/{channel}/{position}     1 = on, else off
				else if (strncmp(resource, "switch", 6) == 0) {

					bool valid = false;
					int channel = atoi(param1);
					int position = atoi(param2);

					if(channel >= 0 && channel < CHANNEL_SIZE) {
						valid = true;
					}

					if(valid) {

						position == 1 ? switchOn(channels[channel]) : switchOff(channels[channel]);

						strcpy(json, json_bracket_open);

						  strcpy_P(string_buffer, (char*)pgm_read_word(&(string_table[idx_json_key_channel])));
						  strcat(json, string_buffer);
						  strcat(json, param1);

						  strcpy_P(string_buffer, (char*)pgm_read_word(&(string_table[idx_json_key_pin])));
						  strcat(json, string_buffer);
						  itoa(channels[channel], string_buffer, 10);
						  strcat(json, string_buffer);

						  strcpy_P(string_buffer, (char*)pgm_read_word(&(string_table[idx_json_key_position])));
						  strcat(json, string_buffer);
						  itoa(digitalRead(channels[channel]), string_buffer, 10);
						  strcat(json, string_buffer);

						strcat(json, json_bracket_close);

						#if DEBUG
							Serial.print("/switch: ");
							Serial.println(json);
						#endif

					}
					else {
						strcpy(json, json_bracket_open);
							strcpy_P(string_buffer, (char*)pgm_read_word(&(string_table[idx_json_error_invalid_channel])));
							strcat(json, string_buffer);
						strcat(json, json_bracket_close);
					}
				}

				// /reboot
				else if (strncmp(resource, "reboot", 6) == 0) {
					#if DEBUG
					  Serial.println("/reboot");
					#endif

					strcpy(json, json_bracket_open);
						strcpy_P(string_buffer, (char*)pgm_read_word(&(string_table[idx_json_reboot_true])));
						strcat(json, string_buffer);
					strcat(json, json_bracket_close);

					reboot = true;
				}

				// /reset
				else if (strncmp(resource, "reset", 5) == 0) {
					#if DEBUG
						Serial.println("/reset");
					#endif

					resetDefaults();

					strcpy(json, json_bracket_open);
						strcpy_P(string_buffer, (char*)pgm_read_word(&(string_table[idx_json_reset_true])));
						strcat(json, string_buffer);
					strcat(json, json_bracket_close);

					reboot = true;
				}

				// /sys
				else if (strncmp(resource, "sys", 3) == 0) {

					strcpy(json, json_bracket_open);

						strcpy_P(string_buffer, (char*)pgm_read_word(&(string_table[idx_hardware_version])));
						strcat(json, string_buffer);

						strcpy_P(string_buffer, (char*)pgm_read_word(&(string_table[idx_firmware_version])));
						strcat(json, string_buffer);

						strcpy_P(string_buffer, (char*)pgm_read_word(&(string_table[idx_json_key_uptime])));
						strcat(json, string_buffer);
						itoa(millis(), string_buffer, 10);
					    strcat(json, string_buffer);

					strcat(json, json_bracket_close);
				}

				else {
					#if DEBUG
					  Serial.println("404");
					#endif
					send404();
					break;
				}

				strcpy_P(string_buffer, (char*)pgm_read_word(&(string_table[idx_http_200])));
				httpClient.println(string_buffer);

				strcpy_P(string_buffer, (char*)pgm_read_word(&(string_table[idx_http_xpowered_by])));
				httpClient.println(string_buffer);

				strcpy_P(string_buffer, (char*)pgm_read_word(&(string_table[idx_http_content_type_json])));
				httpClient.println(string_buffer);

				httpClient.println();
				httpClient.println(json);

				break;
			}
		}
	}

	// give the web browser time to receive the data
	delay(100);

	// close the connection:
	httpClient.stop();

	if(reboot)  {
	  resetFunc();
	  return;
	}
}

void send404() {

	strcpy_P(string_buffer, (char*)pgm_read_word(&(string_table[idx_http_404])));
	httpClient.println(string_buffer);

	#if DEBUG
	  Serial.println(string_buffer);
	#endif

	strcpy_P(string_buffer, (char*)pgm_read_word(&(string_table[idx_http_xpowered_by])));
	httpClient.println(string_buffer);

	httpClient.println();
}

void resetDefaults() {
#if DEBUG
  Serial.println("resetting");
#endif
	EEPROM.write(0, defaultMac[0]);
	EEPROM.write(1, defaultMac[1]);
	EEPROM.write(2, defaultMac[2]);
	EEPROM.write(3, defaultMac[3]);
	EEPROM.write(4, defaultMac[4]);
	EEPROM.write(5, defaultMac[5]);
	EEPROM.write(6, 192);
	EEPROM.write(7, 168);
	EEPROM.write(8, 0);
	EEPROM.write(9, 93);
}

int availableMemory() {
  int free_memory;
  return ((int) __brkval == 0) ? ((int) &free_memory) - ((int) &__bss_end) :
      ((int) &free_memory) - ((int) __brkval);
}

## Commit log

2019-03-01 fix rest param logging
    [main.cpp]
2019-03-06 add documentation. create reset endpoint
    [main.cpp]
2019-03-10 make timer multithreaded
2019-04-05 fix channeol/pin mapping bug
    [main.cpp]
2019-04-05 fix dispene time bug
    [main.cpp]
2019-04-06 rename to cropdroid-room. fix channel 0 dosing bug
    [main.cpp]
2019-04-29 add /switch endpoint
2019-06-12 fix default ip. Add EEPROM_DEBUG flag. Add EEPROM.write call
    [main.cpp]
2020-02-10 add kicad project and final v0.1a artifact
    [bom.csv, cropdroid-doser.kicad_pcb, cropdroid-doser.sch]
2020-02-10 fix kicad nano pinout
    [cropdroid-doser.kicad_pcb]
2020-02-14 kicad doser v0.2a
    [bom.csv, cropdroid-doser.kicad_pcb, cropdroid-doser.sch]
2020-02-21 v0.4a hardware
    [cropdroid-doser.kicad_pcb, cropdroid-doser.sch]
2020-02-21 final v0.4a hardware
    [bom.csv]
2020-02-24 fix switch endpoint
2020-03-01 update kicad cache
2020-03-02 hardware v0.5a
    [bom.csv, cropdroid-doser-B_Cu.dxf, cropdroid-doser-B_Mask.dxf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]
2020-04-13 fix /switch, /reset, and /reboot endpoints. change supported channel count to 14 (from 16)
    [main.cpp]
2020-04-13 replace hard coded json syntax with global variables
    [main.cpp]
2020-04-13 fix rest resource length checks
    [main.cpp]
2021-07-27 fix memory leak and channel size bug. create golang test suite
    [main.cpp]
2024-01-16 Add hardware flow image

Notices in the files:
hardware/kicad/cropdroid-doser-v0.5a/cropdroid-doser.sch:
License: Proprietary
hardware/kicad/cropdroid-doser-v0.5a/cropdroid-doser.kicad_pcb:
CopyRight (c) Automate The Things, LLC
